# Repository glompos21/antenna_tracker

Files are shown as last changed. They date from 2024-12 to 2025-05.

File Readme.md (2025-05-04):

# Mostly 3D printed antenna tracker

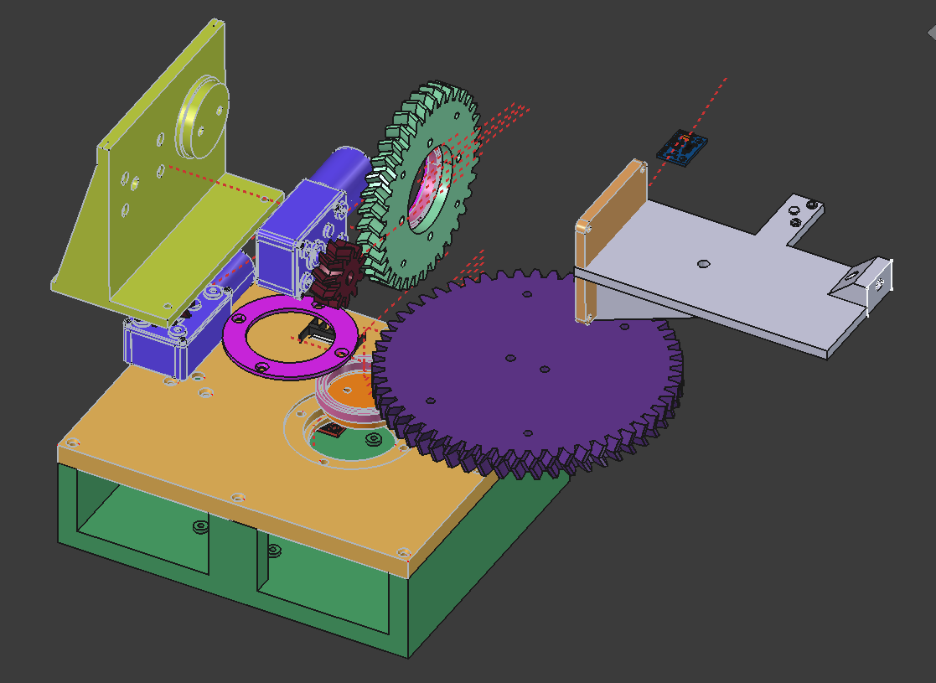
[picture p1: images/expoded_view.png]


The main change from previous version is change into double helix.
Max 1 min for traversing 180o for azimuthal so around 6o/sec

## Parts
- 2x DC Motor Worm Gear Motor 

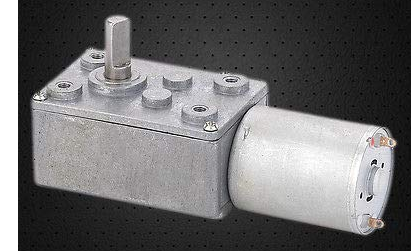
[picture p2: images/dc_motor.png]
foto

- DC motor driver 
- Main electric board 

- 2x 6707-2rs bearings

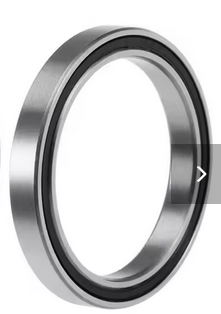
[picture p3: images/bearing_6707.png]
bearing


- 8 x M3x6 (I got a M3x10 and file it)
- 12 x M3x10
- 8 x M3x20
- 8 x M3 nut and washer
- 2x M3x6 Screw without Head  
- 2.5mm drill bit. Used to set the hole for the small_spur_gear_double_helix
- 12x M3 heat insert

# Tolerance
Print the part tolerance_test_print to test the tolerance of your 3D printer for the integral (VarSet.Base_bearing_inside_diameter_with_tolerance) and external (VarSet.Base_bearing_outside_diameter_with_tolerance) diameter of bearing. 
- Change the VarSet.Base_tolerance_outside_circle if the internal base for the bearing is need adjacent (VarSet.Base_bearing_inside_diameter_with_tolerance). 
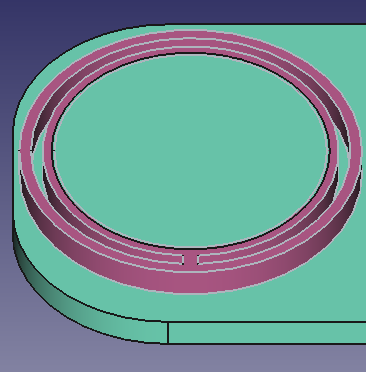
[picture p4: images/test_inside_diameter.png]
internal_base

- Change the VarSet.Base_tolerance_inside_circle if the external base of the bearing need adjacent (VarSet.Base_bearing_outside_diameter_with_tolerance).
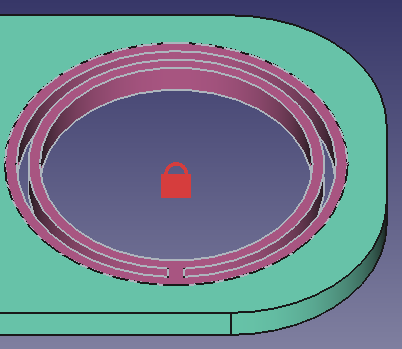
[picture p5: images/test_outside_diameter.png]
outside_base


# Software

Controlling on android: https://github.com/rt-bishop/Look4Sat/

## On Linux
Install:
- gpredict
- HAMLIB https://github.com/Hamlib/Hamlib/wiki/Download#latest-release
Plug the rotator into to a USB port and start the HAMLIB rotator control daemon in a terminal window:
- rotctld -m 202 -r /dev/ttyACM0 -s 9600 -C timeout=500 -vvv
- Where: 202 is the model number for a rotator emulating AMSAT Easycomm II protocol 

## Testing
2 different type of commands
- Easycomm II rotator. Need to be ternamanted with a New Line code.
    - Querey commands send: "AZ EL"
    - Send command: "AZnn.n ELnn.n"
- User commands. NEED to be terminated with Carriege Return (CR)
	- to set to az=100.1 and el=45.4, put on 100.1 45.5<CR>

# L298N Motor Driver Logic Table (1 Motor)

| IN1 | IN2 | Motor State |
|-----|-----|---|
|  1  |  0  | Forward |
|  0  |  1  | Backward |
|  1  |  1  | Brake (Short) |
|  0  |  0  | Stop (Free Run)  |

## Firmware
Based on https://github.com/F4HTB/esp32Rotor
Calibrate the LSM303DLHC sensor: 
- https://www.sarcnet.org/mini-satellite-antenna-rotator-mk1.html -> Calibration Instructions
- https://www.youtube.com/watch?v=oJnpO5Nj7Gc

# Calibration Jig

A calibration jig for the LSM303DLHC. 
See [calibration.md](./firmware/calibration.md) for more info.
You can use a 3d printed [calibration_jig](https://github.com/glompos21/calibration_jig)

## License

Copyright (c) 2024 Kostas Gompakis

Licensed under the MIT license.

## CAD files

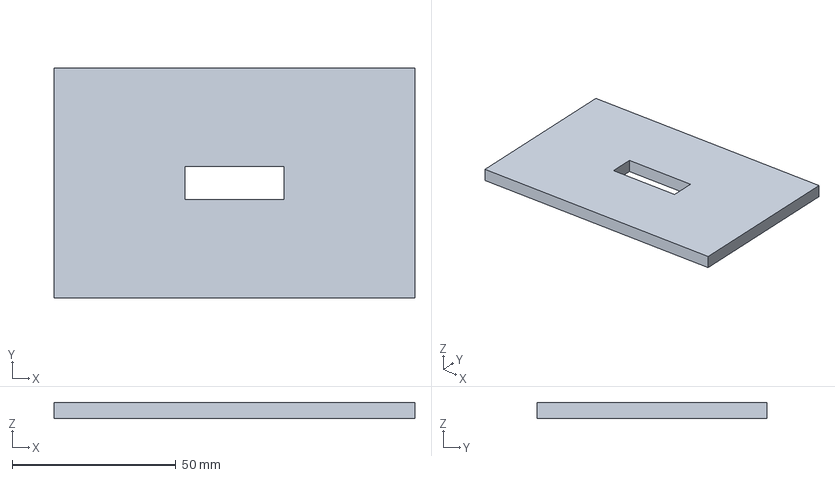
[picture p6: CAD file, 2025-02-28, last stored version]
caribration_jig/3mf/calibration_jig-Assemblybase001.3mf
110.2 x 70.1 x 5.00 mm

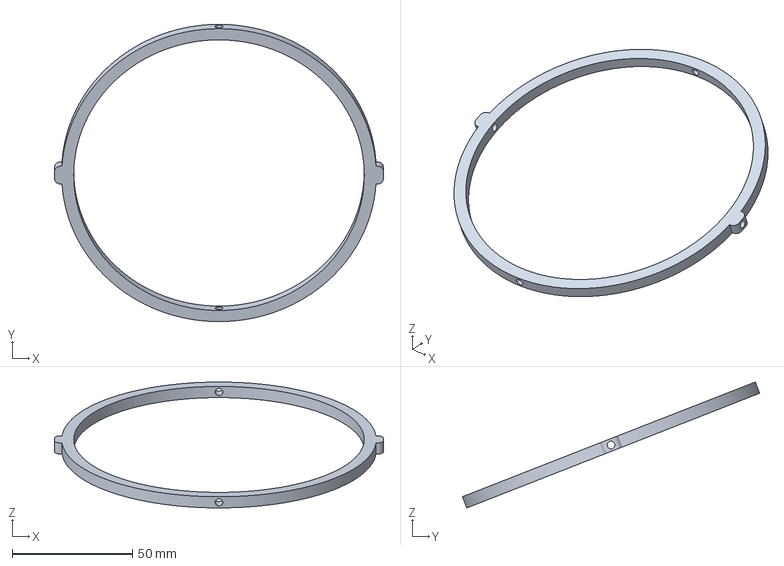
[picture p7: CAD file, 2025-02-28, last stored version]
caribration_jig/3mf/calibration_jig-Assemblythird_circle001.3mf
137.0 x 123.8 x 52.4 mm

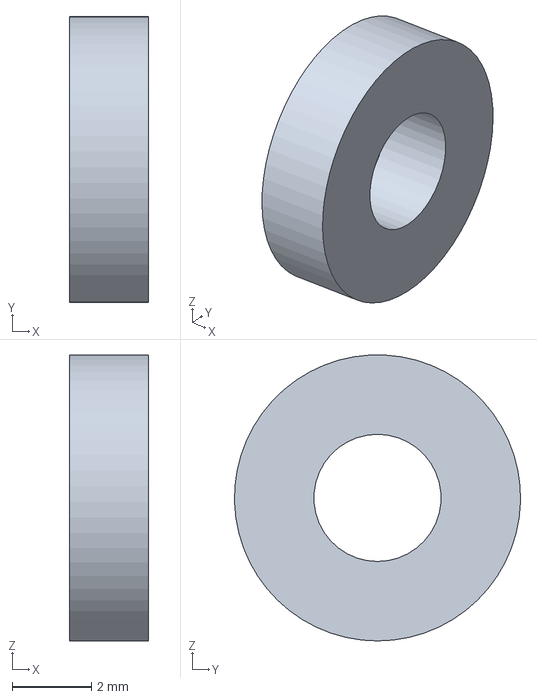
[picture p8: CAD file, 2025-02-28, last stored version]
caribration_jig/3mf/calibration_jig-Assemblyspace001.3mf
2.00 x 7.20 x 7.19 mm

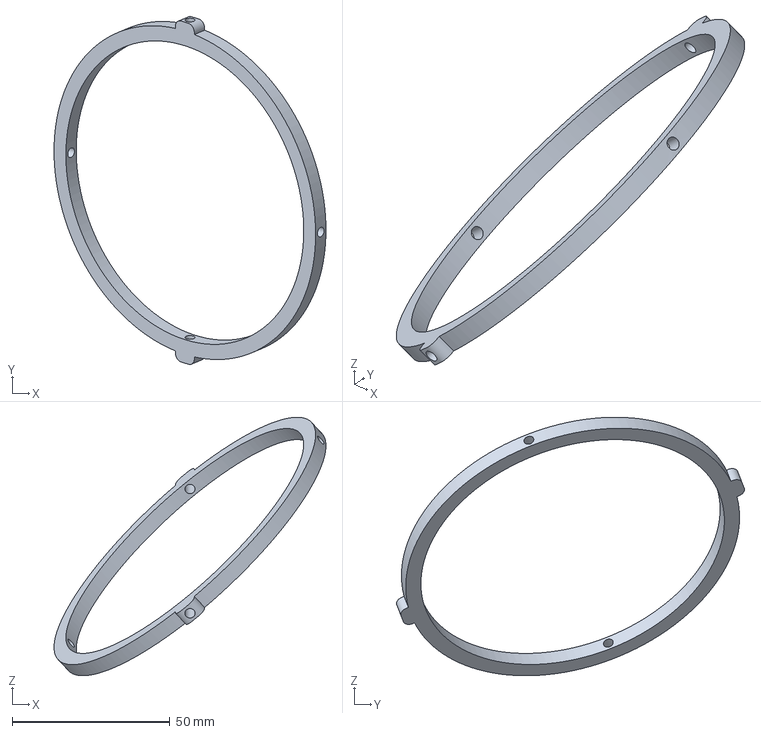
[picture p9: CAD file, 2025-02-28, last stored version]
caribration_jig/3mf/calibration_jig-Assemblysecond_cicle001.3mf
86.2 x 110.3 x 81.9 mm

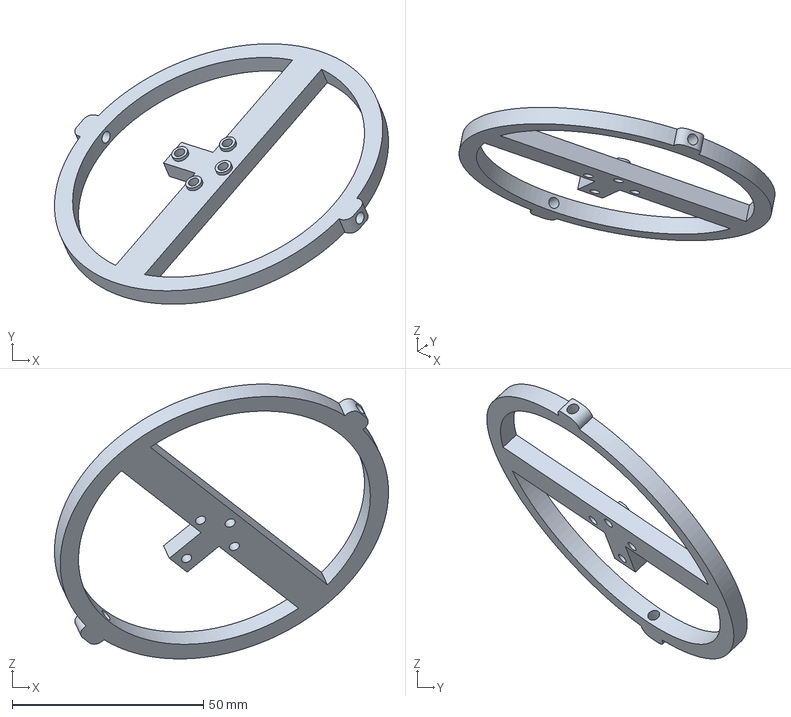
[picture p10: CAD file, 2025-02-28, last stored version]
caribration_jig/3mf/calibration_jig-Assemblyfirst_circle001.3mf
87.2 x 68.0 x 71.8 mm

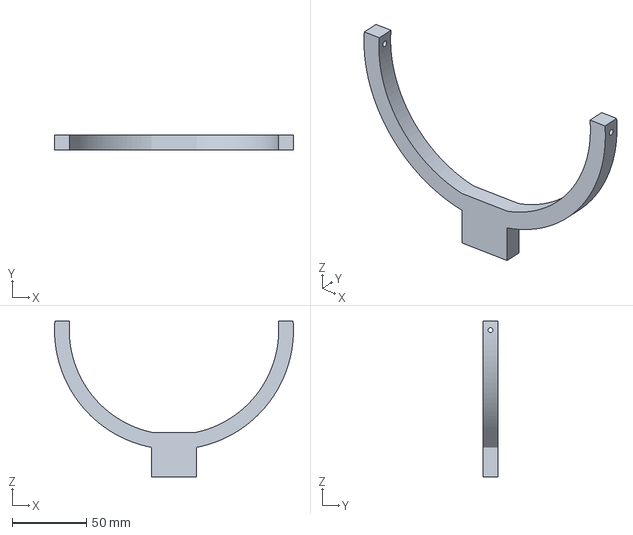
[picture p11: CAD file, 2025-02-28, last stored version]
caribration_jig/3mf/calibration_jig-Assemblybase_outside001.3mf
160.9 x 10.0 x 104.9 mm

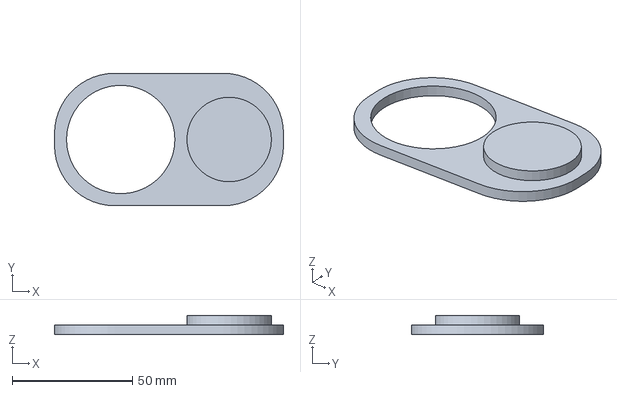
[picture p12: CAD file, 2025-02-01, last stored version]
3mf/antenna_tracker_alternative_gears_v0.5.3-tolerance_test_printBody.3mf
95.1 x 55.0 x 8.00 mm

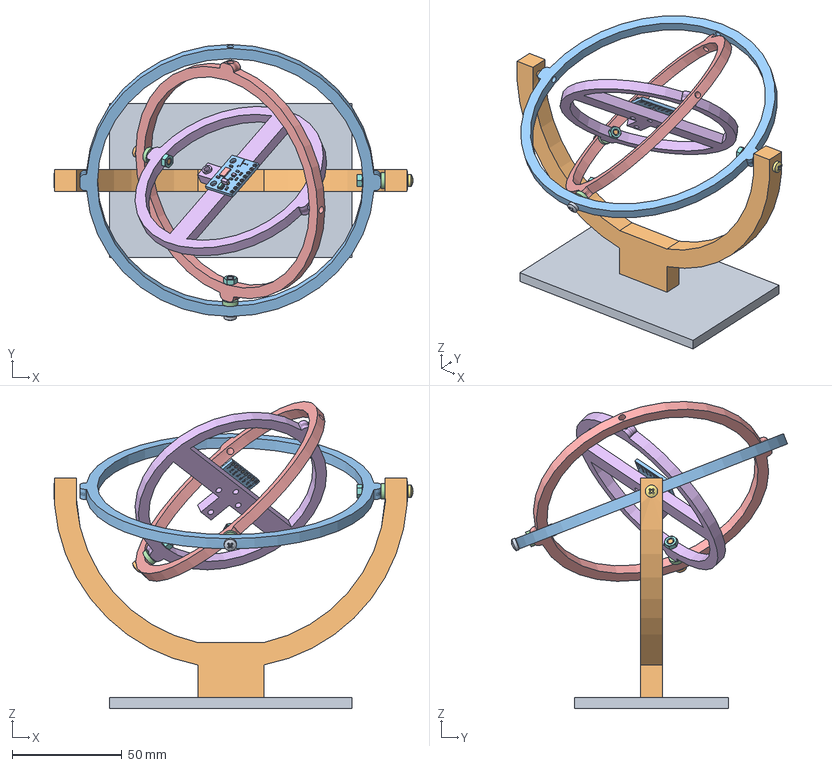
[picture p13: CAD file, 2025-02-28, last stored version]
caribration_jig/calibration_jig.FCStd
163.4 x 125.6 x 139.7 mm
base
base_outside
third_circle
space x 3
second_cicle
first_circle
M3x23-Screw
M3-Nut x 3
M3x18-Screw
M3x18-Screw003
PCB
trou1
trou002
trou003
trou004
trou005
trou006
trou007
trou008
Text_VIN
Text_VIN001
Text_VIN002
Text_3.3V
Text_3.3V001
Text_3.3V002
Text_3.3V003
Text_GND
Text_GND001
Text_GND002
Text_SCL
Text_SCL001
Text_SCL002
Text_SDA
Text_SDA001
Text_SDA002
Text_INT2
Text_INT003
Text_INT004
Text_INT005
Text_INT1
Text_INT007
Text_INT008
Text_INT009
Text_DRDY
Text_DRDY001
Text_DRDY002
Text_DRDY003
R_0603_1608Metric
R_0603_1608Metric001
R_0603_1608Metric002
R_0603_1608Metric003
C_0603_1608Metric001
C_0603_1608Metric003
Corps002
Corps001 (Mirror #1)
C_0603_1608Metric004
C_0603_1608Metric005
Text_ITGMPU
Text_ITGMPU001
Text_ITGMPU002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

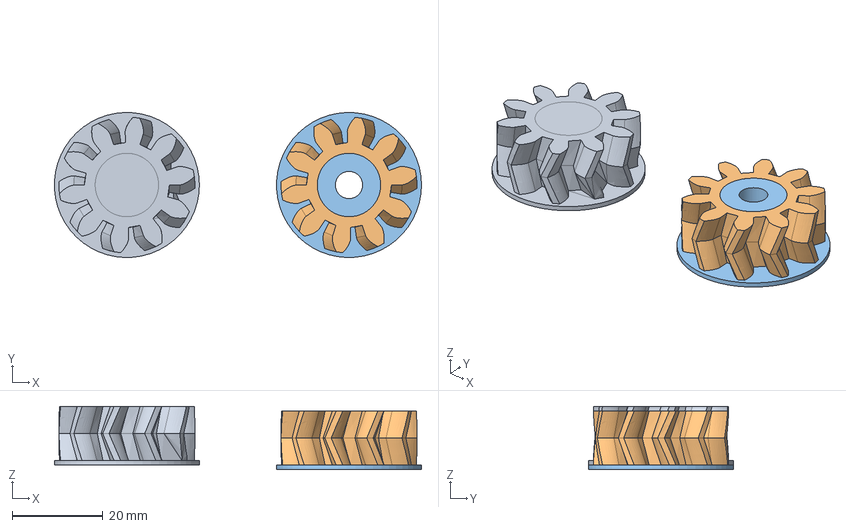
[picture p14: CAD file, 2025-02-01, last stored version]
possible_issue.FCStd
81.0 x 32.0 x 14.0 mm
InvoluteGear003

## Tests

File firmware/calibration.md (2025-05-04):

From https://www.youtube.com/watch?v=2W2W5A5Gk1E. Put tape over the buzzer, it will take 3-8min.

1. place sensor facing magnetic north x->

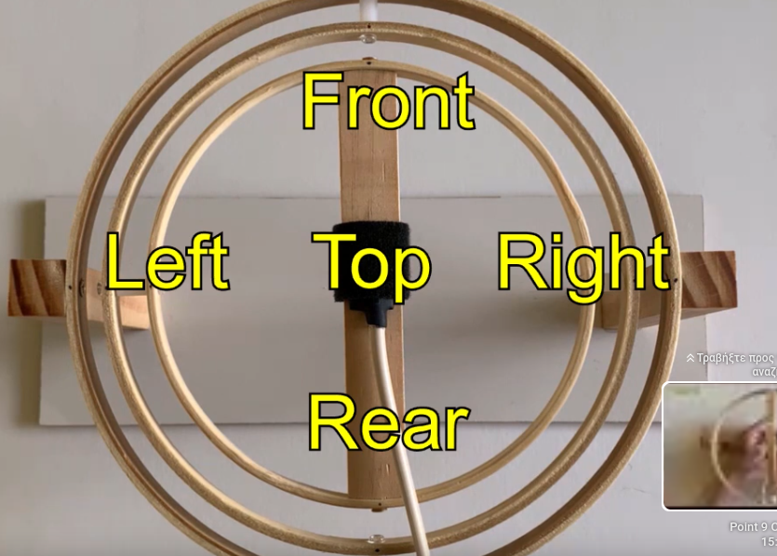
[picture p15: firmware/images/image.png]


2. rough calibration  moving the sensor in 2 horizontal axis

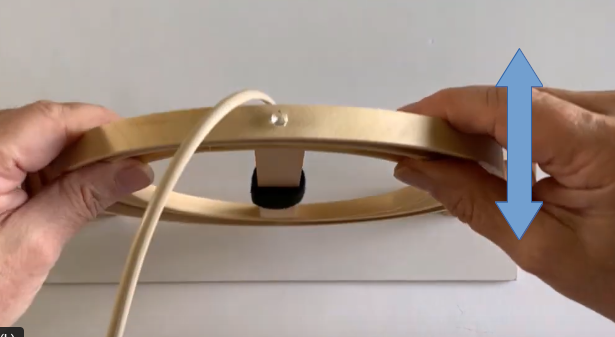
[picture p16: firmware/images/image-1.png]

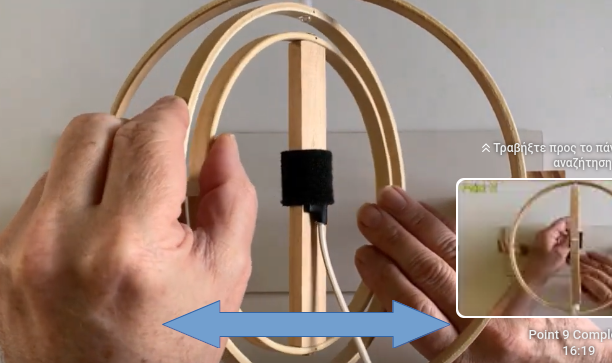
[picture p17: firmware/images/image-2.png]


3. Starting 12 calibration points: we point the front side of the sensor to a point halfway between the vertical and our local magnetic inclination and wait until sarc track stops beeping we then point the front side of the sensor vertically we search around that point until sarc track stops beeping

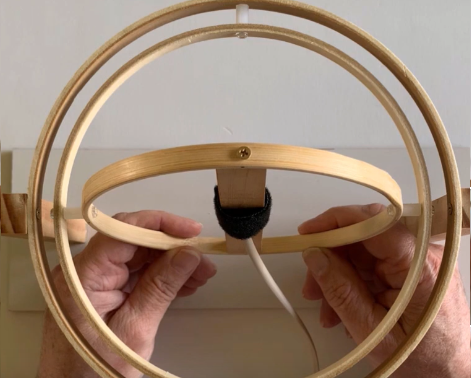
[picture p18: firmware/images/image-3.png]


4. Point No1: the sensor verticaly and waiting till the beep ends. Move around 10o around the vertical 

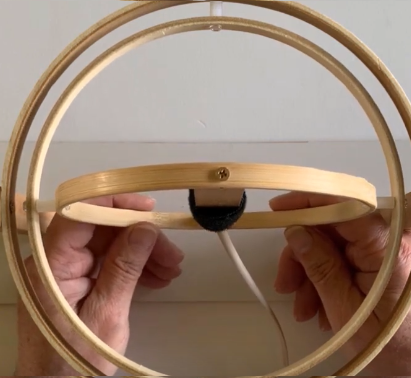
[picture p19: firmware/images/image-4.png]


5. Point No2: our local magnetic inclination. Mover around 10o on cerfucar on that point

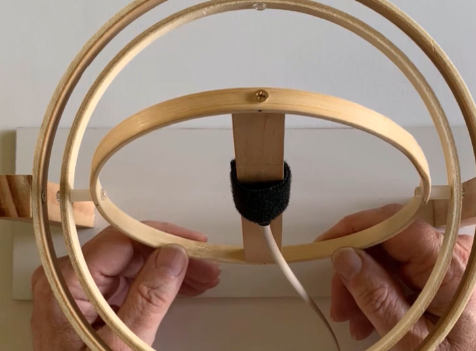
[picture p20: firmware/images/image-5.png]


6. Point No3-1: halfway between the vertical and our local magnetic inclination. Mover around 10o on cerfucar on that point

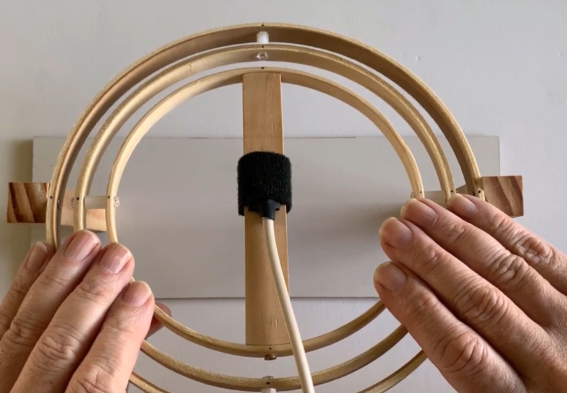
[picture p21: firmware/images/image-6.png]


7. Point No4: Mover sensor verticaly. Mover around 10o on cerfucar on that point

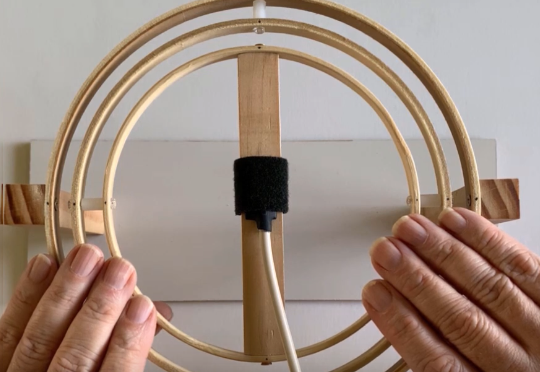
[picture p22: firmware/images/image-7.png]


8. Point No5: the top side of the sensor to our local magnetic inclination we search around that point until sarc track stops beeping

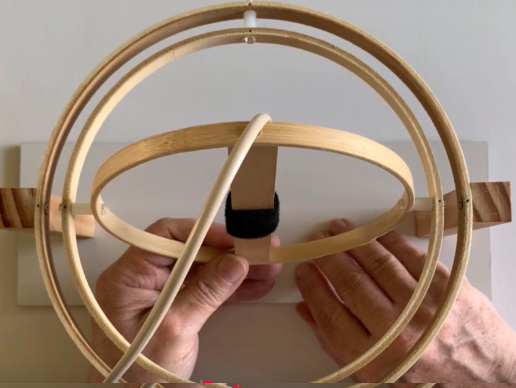
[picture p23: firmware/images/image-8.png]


9. Point No5-2: pointing horizontaly until stop beeping

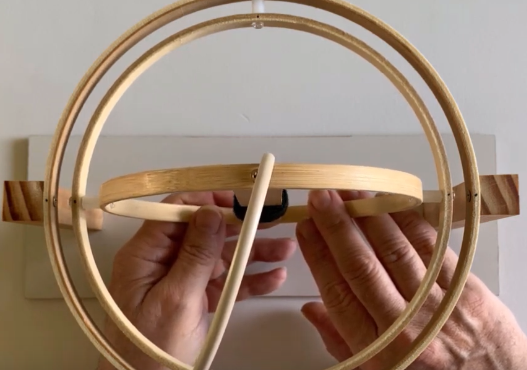
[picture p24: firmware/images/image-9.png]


10. Point 6. we point the rear side of the sensor to a point halfway between the vertical and our local magnetic inclination 



11. Point 7: point the bottom side of the sensor to a point halfway between the vertical and our local magnetic inclination and wait until sarc track stops beeping



12. Point 7-1: point the sensor verticaly



13. Point 8: point the bottom side of the sensor to a our local magnetic inclination and wait until sarc track stops beeping



14. Point 9:  left side of the sensor to a point halfway between the 
vertical and our local magnetic inclination and wait until sarc track stops beeping



14. Point 9-2 :left side of the sensor verticaly



15. Point 10:  left side of the sensor to our local magnetic inclination and wait until sarc track stops beeping



16. Point 11:  right side of the sensor to a point halfway between the 
vertical and our local magnetic inclination and wait until sarc track stops beeping



17. Point 12:  right side of the sensor to our local magnetic inclination and wait until sarc track stops beeping

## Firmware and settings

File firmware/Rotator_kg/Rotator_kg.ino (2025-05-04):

//Includes
#include <Arduino.h>
#include <Wire.h>
#include <Preferences.h>
#include <LSM303.h>

#include "timer.h"
#include "mot.h"


// #include "esp_bt_main.h"
// #include "esp_bt_device.h"
// #include "BluetoothSerial.h"

// ////////Bluetooth
// #if !defined(CONFIG_BT_ENABLED) || !defined(CONFIG_BLUEDROID_ENABLED)
// #error Bluetooth is not enabled! Please run `make menuconfig` to and enable it
// #endif
// BluetoothSerial SerialBT;
// ////////!Bluetooth

Preferences preferences;
LSM303 compass;

#define SerialPort Serial  //Please uncomment this line to use the USB port.
//#define SerialPort Serial1        //Please uncomment this line to use the TTL port.
#define WINDUP_LIMIT 450  //Sets the total number of degrees azimuth rotation in any direction before resetting to zero
//Motor pins - Don't change
const int azFwdPin = 25;
const int azRevPin = 26;
const int elFwdPin = 32;
const int elRevPin = 33;

// //Motor drive gains. These set the amount of motor drive close to the set point
// const int azGain = 25;  //Azimuth motor gain
// const int elGain = 25;  //Elevation motor gain
// //Filter constants
// const float azAlpha = 0.25;    //Alpha value for AZ motor filter: Decrease to slow response time and reduce motor dither.
// const float elAlpha = 0.25;    //Alpha value for EL motor filter: Decrease to slow response time and reduce motor dither.

//Modes
enum Modes { tracking,
             monitoring,
             calibrating,
             debugging,
             pausing,
             manual };  //Rotator controller modes

//Global variables
float az;        //Antenna azimuth
float el;        //Antenna elevation
String line;     //Command line
float azSet;     //Antenna azimuth set point
float elSet;     //Antenna elevation set point
float azLast;    //Last antenna azimuth reading
float elLast;    //Last antenna element reading
float azWindup;  //Antenna windup angle from startup azimuth position
float azOffset;  //Antenna azimuth offset for whole revolutions
bool windup;     //Antenna windup condition
float azError;   //Antenna azimuth error
float elError;   //Antenna elevation error
Modes mode;      //Rotator mode
int calibration_counter = 0;
float magnetic_declination = 0;
//Objects

//Motor driver object: Mot xxMot(Driver-Type, Filter-Alpha, Gain, Fwd-Pin, Rev/Dir-Pin)
Mot azMot(-1, -1, azFwdPin, azRevPin);  //AZ motor driver object
Mot elMot(-1, -1, elFwdPin, elRevPin);  //EL motor driver object

//Non-blocking Timer object
Timer t1(100);


//Functions
void reset(bool getCal) {
  //Reset the rotator, initialize its variables and optionally get the stored calibration
  azSet = 0.0;
  elSet = 0.0;
  line = "";
  azLast = 0.0;
  elLast = 0.0;
  azWindup = 0.0;
  azOffset = 0.0;
  mode = tracking;
  windup = false;
  // if (getCal) restore();
  azError = 0.0;
  elError = 0.0;
  t1.reset(100);
  printCal();
}

float diffAngle(float a, float b) {
  //Calculate the acute angle between two angles in -180..180 degree format
  float diff = a - b;
  if (diff < -180) diff += 360;
  if (diff > 180) diff -= 360;
  return diff;
}

void save() {
  // magnetic_declination
  preferences.begin("calibration", false);  // namespace "calibration", RW mode
  // Save the calibration data structure to preferences
  // preferences.putBytes("lsm_cal", &lsm.cal, sizeof(lsm.cal));
  preferences.end();
}

void restore() {
  preferences.begin("calibration", true);  // namespace "calibration", read-only mode
  // preferences.getBytes("lsm_cal", &lsm.cal, sizeof(lsm.cal));
  preferences.end();
}


void setLSMCalData() {
  compass.m_min = (LSM303::vector<int16_t>){ -444, -475, -1455 };
  compass.m_max = (LSM303::vector<int16_t>){ +824, +486, -641 };
}


void printCal(void) {
  char buffer[200];  // Ensure this is large enough for your full output string

  SerialPort.println(buffer);
}
void printMon(float az, float el, float azSet, float elSet, float azWindup, float azError, float elError) {
  //Print the monitor data
  SerialPort.print("printMon, az:");
  SerialPort.print(az, 2);
  SerialPort.print(",azSet:");
  SerialPort.print(azSet, 2);
  SerialPort.print(",azError:");
  SerialPort.print(azError, 2);
  SerialPort.print(",el:");
  SerialPort.print(el, 2);
  SerialPort.print(",elSet:");
  SerialPort.print(elSet, 2);
  SerialPort.print(",elError:");
  SerialPort.print(elError, 2);
  SerialPort.print(",azWindup:");
  SerialPort.print(azWindup, 2);
  SerialPort.print(",windup:");
  SerialPort.println(windup);
}

void printAzEl() {
  //Print the rotator feedback data in Easycomm II format
  SerialPort.print("AZ");
  SerialPort.print((az < 0) ? (az + 360) : az, 1);
  SerialPort.print(" EL");
  SerialPort.print(el, 1);
  SerialPort.print("\n");
}

void calibrate() {
}

void getWindup(bool *windup, float *azWindup, float *azOffset, float *azLast, float *elLast, float az, float elSet) {
  //Get the accumulated windup angle from the home position (startup or last reset position) and set the windup state if greater than the limit.
  //Get the raw difference angle between the current and last azimuth reading from the sensor
  float azDiff = az - *azLast;

  //Detect crossing South: azDiff jumps 360 for a clockwise crossing or -360 for an anticlockwise crossing
  //Increment the azimuth offset accordingly
  if (azDiff < -180) *azOffset += 360;
  if (azDiff > 180) *azOffset -= 360;

  //Save the current azimuth reading for the next iteration
  *azLast = az;

  //Compute the azimuth wind-up angle, i.e. the absolute number of degrees from the home position
  *azWindup = az + *azOffset;

  //Detect a windup condition where the antenna has rotated more than 450 degrees from home
  if (abs(*azWindup) > WINDUP_LIMIT) *windup = true;  //Set the windup condition - it is reset later when the antenna nears home

  //Perform the anti-windup procedure at the end of each pass - This is overkill unless you absolutely don't want anti-windup during a pass
  //  if (elSet <= 0)
  //    if (elLast > 0)
  //      if (mode == tracking) {
  //        *windup = true;
  //      }

  //Save the current elevation reading for the next iteration
  *elLast = elSet;
}


void getAzElError(float *azError, float *elError, bool *windup, float *azSet, float *elSet, float az, float el) {
  //Compute the azimuth and elevation antenna pointing errors, i.e. angular offsets from set positions
  //Compute the azimuth antenna pointing error: Normally via the shortest path; opposite if windup detected.
  if (*windup) {  //Check for a windup condition
    //To unwind the antenna set an azError in the appropriate direction to home
    *azError = constrain(azWindup, -180, 180);  //Limit the maximum azimuth error to -180..180 degrees
    //Cancel the windup condition when the antenna is within 180 degrees of home (Actually 175 degrees to avoid rotation direction ambiguity)
    //Set a zero home position by default, but return azumith control to the computer if still connected
    if (abs(*azError) < 175) *windup = false;  //Cancel windup and permit computer control
  } else {
    //Compute the normal azimuth antenna pointing error when there is no windup condition
    *azError = diffAngle(az, *azSet);
  }

  //Compute the elevation antenna pointing error
  *elError = diffAngle(el, *elSet);
}

void processPosition() {
  //Perform the main operation of positioning the rotator under different modes
  //Read the accelerometer and magnetometer

  compass.read();
  az = compass.heading() + magnetic_declination;
  el = (atan2(compass.a.x, compass.a.z) * -180.0) / M_PI;

  switch (mode) {
    case debugging:
      // printDebug();  //Print the raw sensor data for debug purposes
      SerialPort.print(az);
      SerialPort.print(",");
      SerialPort.println(el);
      break;
    case calibrating:
      calibrate();  //Process calibration data
      break;
    case pausing:
      azMot.halt();  //Stop the AZ motor
      elMot.halt();  //Stop the EL motor
      azError = 0;
      elError = 0;
      break;
    case manual:
      printMon(az, el, azSet, elSet, azWindup, azError, elError);
      break;
    default:
      if (azSet == 0 && elSet == 0) {
        azError = 0;
        elError = 0;
      } else {
        // getWindup(&windup, &azWindup, &azOffset, &azLast, &elLast, az, elSet);   //Get the AZ windup angle and windup state
        // if (mode == demonstrating) getAzElDemo(&azSet, &elSet, &azInc, &elInc);  //Set the AZ and EL automatically if in demo mode
        getAzElError(&azError, &elError, &windup, &azSet, &elSet, az, el);  //Get the antenna pointing error
      }
      if (mode == monitoring) printMon(az, el, azSet, elSet, azWindup, azError, elError);  //Print the data if in monitor mode
  }
  if (isnan(azError)) azError = 0;
  if (isnan(elError)) elError = 0;
}

void processMotors() {
  //Drive the motors to reduce the azimuth and elevation error to zero
  azMot.drive(azError);
  elMot.drive(elError);
}

void processUserCommands(String line) {
  //Process user commands
  //User command type 1: r, b, m, c, a, d, s, d, h, p or e<decl> followed by a carriage return
  //User command type 2: <az> <el> followed by a carriage return
  String param;    //Parameter value
  int firstSpace;  //Position of the first space in the command line
  int secondSpace;
  String azString;
  String elString;
  char command = line.charAt(0);  //Get the first character
  switch (command) {              //Process type 1 user commands
    case 'r':                     //Reset command
      SerialPort.println("Reset in progress");
      reset(true);  //Reset the rotator and load calibration from EEPROM
      SerialPort.println("Reset complete");
      break;
    case 'b':  //Debug command
      SerialPort.println("Debugging in progress: Press 'a' to abort");
      mode = debugging;
      t1.reset(100);
      break;
    case 'm':  //Monitor command
      SerialPort.println("Monitoring in progress: Press 'a' to abort");
      mode = monitoring;
      t1.reset(100);
      break;
    case 'c':  //Calibrate command
      SerialPort.println("Calibration in progress: Press 'a' to abort or 's' to save");
      reset(false);  //Reset the rotator, but don't load calibration from EEPROM
      mode = calibrating;
      t1.reset(50);
      break;
    case 'a':  //Abort command
      mode = tracking;
      t1.reset(100);
      reset(true);
      SerialPort.println("Function aborted");
      break;
    case 'e':                     //Magnetic declination command
      param = line.substring(1);  //Get the second parameter
      magnetic_declination = param.toFloat();
      break;
    case 's':  //Save command
      if (mode == calibrating) {
        save();
        reset(true);
        SerialPort.println("Calibration saved");
        printCal();
      } else {
        SerialPort.println("Not at Calibration mode");
      }
      break;
    case 'g':  // Go to
      mode = manual;
      firstSpace = line.indexOf(' ');              // Index of first space
      param = line.substring(firstSpace + 1);      // Get substring after 'g '
      secondSpace = param.indexOf(' ');            // Find space between az and el
      azString = param.substring(0, secondSpace);  // Extract az value
      azError = azString.toFloat();                // Parse azimuth

      elString = param.substring(secondSpace + 1);  // Extract el value
      elError = elString.toFloat();                 // Parse elevation
      break;

    case 'h':  //Help command
      SerialPort.println("Commands:");
      SerialPort.println("az el -(0..360 0..90)");
      SerialPort.println("r -Reset");
      SerialPort.println("eNN.N -MagDecl");
      SerialPort.println("c -Calibrate");
      SerialPort.println("s -Save");
      SerialPort.println("a -Abort");
      SerialPort.println("b -Debug");
      SerialPort.println("m -Monitor");
      SerialPort.println("p -Pause");
      SerialPort.println("g +-az +-el - Go to +-az +-el ie g 1 -3 -> move az: +1 el:-3");
      break;
    case 'p':  //Pause command
      if (mode == pausing) {
        mode = tracking;
      } else {
        mode = pausing;
        SerialPort.println("Paused");
      }
      break;
    default:  //Process type 2 user commands
      mode = tracking;
      firstSpace = line.indexOf(' ');          //Get the index of the first space
      param = line.substring(0, firstSpace);   //Get the first parameter
      azSet = param.toFloat();                 //Get the azSet value
      param = line.substring(firstSpace + 1);  //Get the second parameter
      elSet = param.toFloat();                 //Get the elSet value
  }
}
// printMon: nan,nan,0,0,nan,0,nan,nan
void processEasycommCommands(String line) {
  //Process Easycomm II rotator commands
  //Easycomm II position command: AZnn.n ELnn.n UP000 XXX DN000 XXX\n
  //Easycomm II query command: AZ EL \n
  String param;                    //Parameter value
  int firstSpace;                  //Position of the first space in the command line
  int secondSpace;                 //Position of the second space in the command line
  if (line.startsWith("AZ EL")) {  //Query command received
    printAzEl();                   //Send the current Azimuth and Elevation
  } else {
    if (line.startsWith("AZ")) {                            //Position command received: Parse the line.
      firstSpace = line.indexOf(' ');                       //Get the position of the first space
      secondSpace = line.indexOf(' ', firstSpace + 1);      //Get the position of the second space
      param = line.substring(2, firstSpace);                //Get the first parameter
      azSet = param.toFloat();                              //Set the azSet value
      if (azSet > 180) azSet = azSet - 360;                 //Convert 0..360 to -180..180 degrees format
      param = line.substring(firstSpace + 3, secondSpace);  //Get the second parameter
      elSet = param.toFloat();                              //Set the elSet value
    }
  }
}

void processCommands(void) {
  //Process incoming data from the control computer
  //User commands are entered by the user and are terminated with a carriage return
  //Easycomm commands are generated by a tracking program and are terminated with a line feed
  while (SerialPort.available() > 0) {
    char ch = SerialPort.read();  //Read a single character from the serial buffer
    switch (ch) {
      case 13:                      //Carriage return received
        processUserCommands(line);  //Process user commands
        line = "";                  //Command processed: Clear the command line
        break;
      case 10:                          //Line feed received
        processEasycommCommands(line);  //Process Easycomm commands
        line = "";                      //Command processed: Clear the command line
        break;
      default:       //Any other character received
        line += ch;  //Add this character to the command line
        break;
    }
  }


  // while (SerialBT.available() > 0) {
  //   char ch = SerialBT.read();  //Read a single character from the serial buffer
  //   switch (ch) {
  //     case 13:                      //Carriage return received
  //       processUserCommands(line);  //Process user commands
  //       line = "";                  //Command processed: Clear the command line
  //       break;
  //     case 10:                          //Line feed received
  //       processEasycommCommands(line);  //Process Easycomm commands
  //       line = "";                      //Command processed: Clear the command line
  //       break;
  //     default:       //Any other character received
  //       line += ch;  //Add this character to the command line
  //       break;
  //   }
  // }
}


// void callback(esp_spp_cb_event_t event, esp_spp_cb_param_t *param) {
//   switch (event) {
//     case ESP_SPP_SRV_OPEN_EVT:
//       SerialPort.println("BT Connected");
//       // beep(40, 5);
//       break;
//     case ESP_SPP_CLOSE_EVT:
//       SerialPort.println("BT Disconnected");
//       // beep(400, 2);
//       break;
//     default:
//       break;
//   }
// }

// void printDeviceAddress() {
//   const uint8_t *point = esp_bt_dev_get_address();
//   for (int i = 0; i < 6; i++) {
//     char str[3];
//     sprintf(str, "%02X", (int)point[i]);
//     SerialPort.print(str);
//     if (i < 5) {
//       SerialPort.print(":");
//     }
//   }
//   SerialPort.print("\n");
// }

void testMotor() {
  int delay_ms = 5000;
  int _drive = 40.;
  read_print_sensor();
  azMot.drive(_drive);
  delay(delay_ms);
  read_print_sensor();
  azMot.drive(-1 * _drive);
  delay(delay_ms);
  azMot.drive(0.0);
  read_print_sensor();
  elMot.drive(_drive);
  delay(delay_ms);
  read_print_sensor();
  elMot.drive(-1 * _drive);
  delay(delay_ms);
  elMot.drive(0.0);
}

void read_print_sensor() {
  compass.read();
  //Get the antenna AZ and EL
  az = compass.heading() + magnetic_declination;
  el = (atan2(compass.a.x, compass.a.z) * -180.0) / M_PI;
  SerialPort.print("az:");

  SerialPort.print(az);
  SerialPort.print(",");
  SerialPort.print(",el:");
  SerialPort.println(el);
}

void setup() {
  //Initialize the system
  //Reset the rotator and load configuration from EEPROM
  reset(true);
  //Initialize the serial port
  SerialPort.begin(9600);

  // SerialBT.register_callback(callback);
  // SerialBT.begin("Glompos21_ESP32_Rotor");
  // SerialPort.print("\nYou can pair bluetooth on:");
  // printDeviceAddress();
  SerialPort.println("\nGlompos21_ESP32_Rotor");
  //Initialize the sensor
  Wire.begin();
  compass.init();
  compass.enableDefault();
  azMot.halt();
  elMot.halt();
  setLSMCalData();
  read_print_sensor();
  SerialPort.println("starting loop...");
}


void loop() {
  //Repeat continuously
  processCommands();             //Process commands from the control computer
  t1.execute(&processPosition);  //Process position only periodically
  processMotors();               //Process motor drive

  // testMotor();
}









// void printCal(void) {
//   //Print the calibration data
//   SerialPort.print("md:");
//   SerialPort.print(lsm.cal.md, 1);
//   SerialPort.print(",");
//   SerialPort.print("me.i:");
//   SerialPort.print(lsm.cal.me.i, 1);
//   SerialPort.print(",");
//   SerialPort.print("me.j:");
//   SerialPort.print(lsm.cal.me.j, 1);
//   SerialPort.print(",");
//   SerialPort.print("me.k:");
//   SerialPort.print(lsm.cal.me.k, 1);
//   SerialPort.print(",");
//   SerialPort.print("ge.i:");
//   SerialPort.print(lsm.cal.ge.i, 1);
//   SerialPort.print(",");
//   SerialPort.print("ge.j:");
//   SerialPort.print(lsm.cal.ge.j, 1);
//   SerialPort.print(",");
//   SerialPort.print("ge.k:");
//   SerialPort.print(lsm.cal.ge.k, 1);
//   SerialPort.print(",");
//   SerialPort.print("ms.i:");
//   SerialPort.print(lsm.cal.ms.i, 1);
//   SerialPort.print(",");
//   SerialPort.print("ms.j:");
//   SerialPort.print(lsm.cal.ms.j, 1);
//   SerialPort.print(",");
//   SerialPort.print("ms.k:");
//   SerialPort.print(lsm.cal.ms.k, 1);
//   SerialPort.print(",");
//   SerialPort.print("gs.i:");
//   SerialPort.print(lsm.cal.gs.i, 1);
//   SerialPort.print(",");
//   SerialPort.print("gs.j:");
//   SerialPort.print(lsm.cal.gs.j, 1);
//   SerialPort.print(",");
//   SerialPort.print("gs.k:");
//   SerialPort.println(lsm.cal.gs.k, 1);
// }

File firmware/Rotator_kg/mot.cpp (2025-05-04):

// mot.cpp - Motor library.
// Copyright (c) 2015-2018 Julie VK3FOWL and Joe VK3YSP
// For more information please visit http://www.sarcnet.org
// Released under the GNU General Public License.
// Provides DC motor speed and direction control

#include "mot.h"

// Public methods

Mot::Mot(float alpha, int gain, int pin1, int pin2)
  : fil(alpha) {
  // Constructor
  _gain = gain;
  _pin1 = pin1;
  _pin2 = pin2;
  pinMode(_pin1, OUTPUT);
  pinMode(_pin2, OUTPUT);
  analogWrite(_pin1, 0);
  analogWrite(_pin2, 0);
}

void Mot::halt() {
  drive(0.0);
}

// void Mot::drive(float err) {
//   if (abs(err) < 0.5) {
//     digitalWrite(_pin1, LOW);
//     digitalWrite(_pin2, LOW);
//   } else {
//     if (err > 0) {
//       digitalWrite(_pin1, HIGH);
//       digitalWrite(_pin2, LOW);
//     } else {
//       digitalWrite(_pin1, LOW);
//       digitalWrite(_pin2, HIGH);
//     }
//   }
// }

void Mot::drive(float err) {
  int speed = 255;
  int no_movement_under = 5.;
if (err < 10.0) {
    speed = 120;
  } else if (err < 20.0) {
    speed = 180;
  } else {
    speed = 255;
  }

  if (abs(err) < no_movement_under) {
    analogWrite(_pin1, 0);
    analogWrite(_pin2, 0);
  } else {
    if (err > 0) {
      analogWrite(_pin1, speed);
      analogWrite(_pin2, 0);
    } else {
      analogWrite(_pin1, 0);
      analogWrite(_pin2, speed);
    }
  }
}

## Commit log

2025-02-01 change to dual heix gears, add testing print bracker, tolerane adjastment
    [antenna_tracker_alternative_gears_v0.5.3-tolerance_test_printBody.3mf, possible_issue.FCStd]
2025-02-28 calibration jig
    [calibration_jig.FCStd]
2025-02-28 3mf calibration jig
    [calibration_jig-Assemblybase001.3mf, calibration_jig-Assemblybase_outside001.3mf, calibration_jig-Assemblyfirst_circle001.3mf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]
2025-02-28 upgrading main tracker
    [antenna_tracker_alternative_gears_v0.5.3-tolerance_test_printBody.3mf, possible_issue.FCStd]
2025-05-04 move calibration jig to seperate gitrepo https://github.com/glompos21/calibration_jig
    [calibration_jig-Assemblybase001.3mf, calibration_jig-Assemblybase_outside001.3mf, calibration_jig-Assemblyfirst_circle001.3mf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]
2025-05-04 adding calibration instructions
2025-05-04 testing sensor and motor
